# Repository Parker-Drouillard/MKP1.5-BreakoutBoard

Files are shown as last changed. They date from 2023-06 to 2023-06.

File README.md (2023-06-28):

# MKP1.5-BreakoutBoard
A breakout board for supporting dual extrusion &amp; 6 pwm fan control for the Rambo 1.4 

This board supports a Teensy 2.0 slave device to the Rambo 1.4 over Serial. The purpose of this board is to expand the available IO of the Rambo 1.4 to be capable of supporting a dual extrusion system, as well as additional PWM fan controls.

## About this board
This board offers 6 5v fan headers for PWM switching via a darlington array. At this current time, it does not seem the max PWM speed of the Teensy 2.0 is sufficient to run the fans at less than 100% power, so for the time being it is simply a toggle of Off or On.
The board includes a 24V to 5V buck converter, capable of supporting 3A of power, of which only 2A is anticipated to be used. Additionally, 2 ports for PT1000 passthrough, and 2 ports for E3D PT100 Amplifier boards are provided. 
An onboard L298N allows for low voltage switching of 2 independant 24V systems, one of which is being used for the second extruder solenoid, and one will be used in the future fora dynamic extruder pressure motor. Both systems have 2 encontrol pins, 1 for forward, and 1 for reverse.

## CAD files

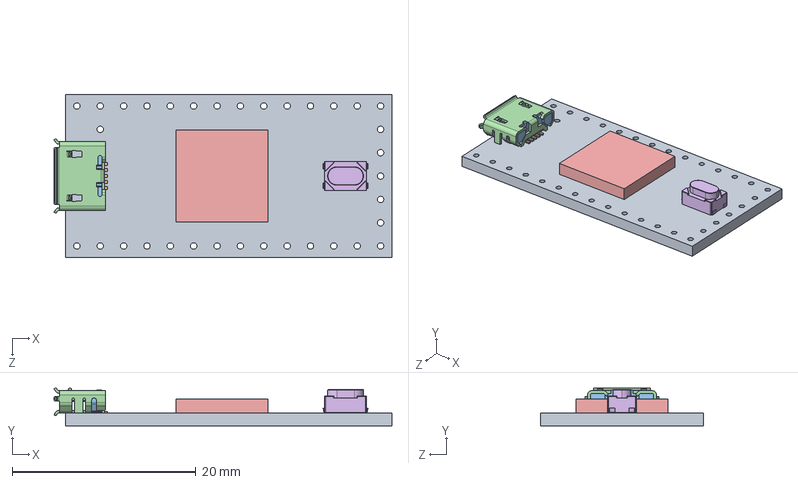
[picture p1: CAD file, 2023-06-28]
teensy.pretty-master/Teensy_4.0_Assembly.STEP
36.8 x 4.12 x 17.7 mm
Teensy_4.0_PCB
Micro USB-B Female 5Pin SMD
NXP iMXRT1062
SKRPACE010 v4

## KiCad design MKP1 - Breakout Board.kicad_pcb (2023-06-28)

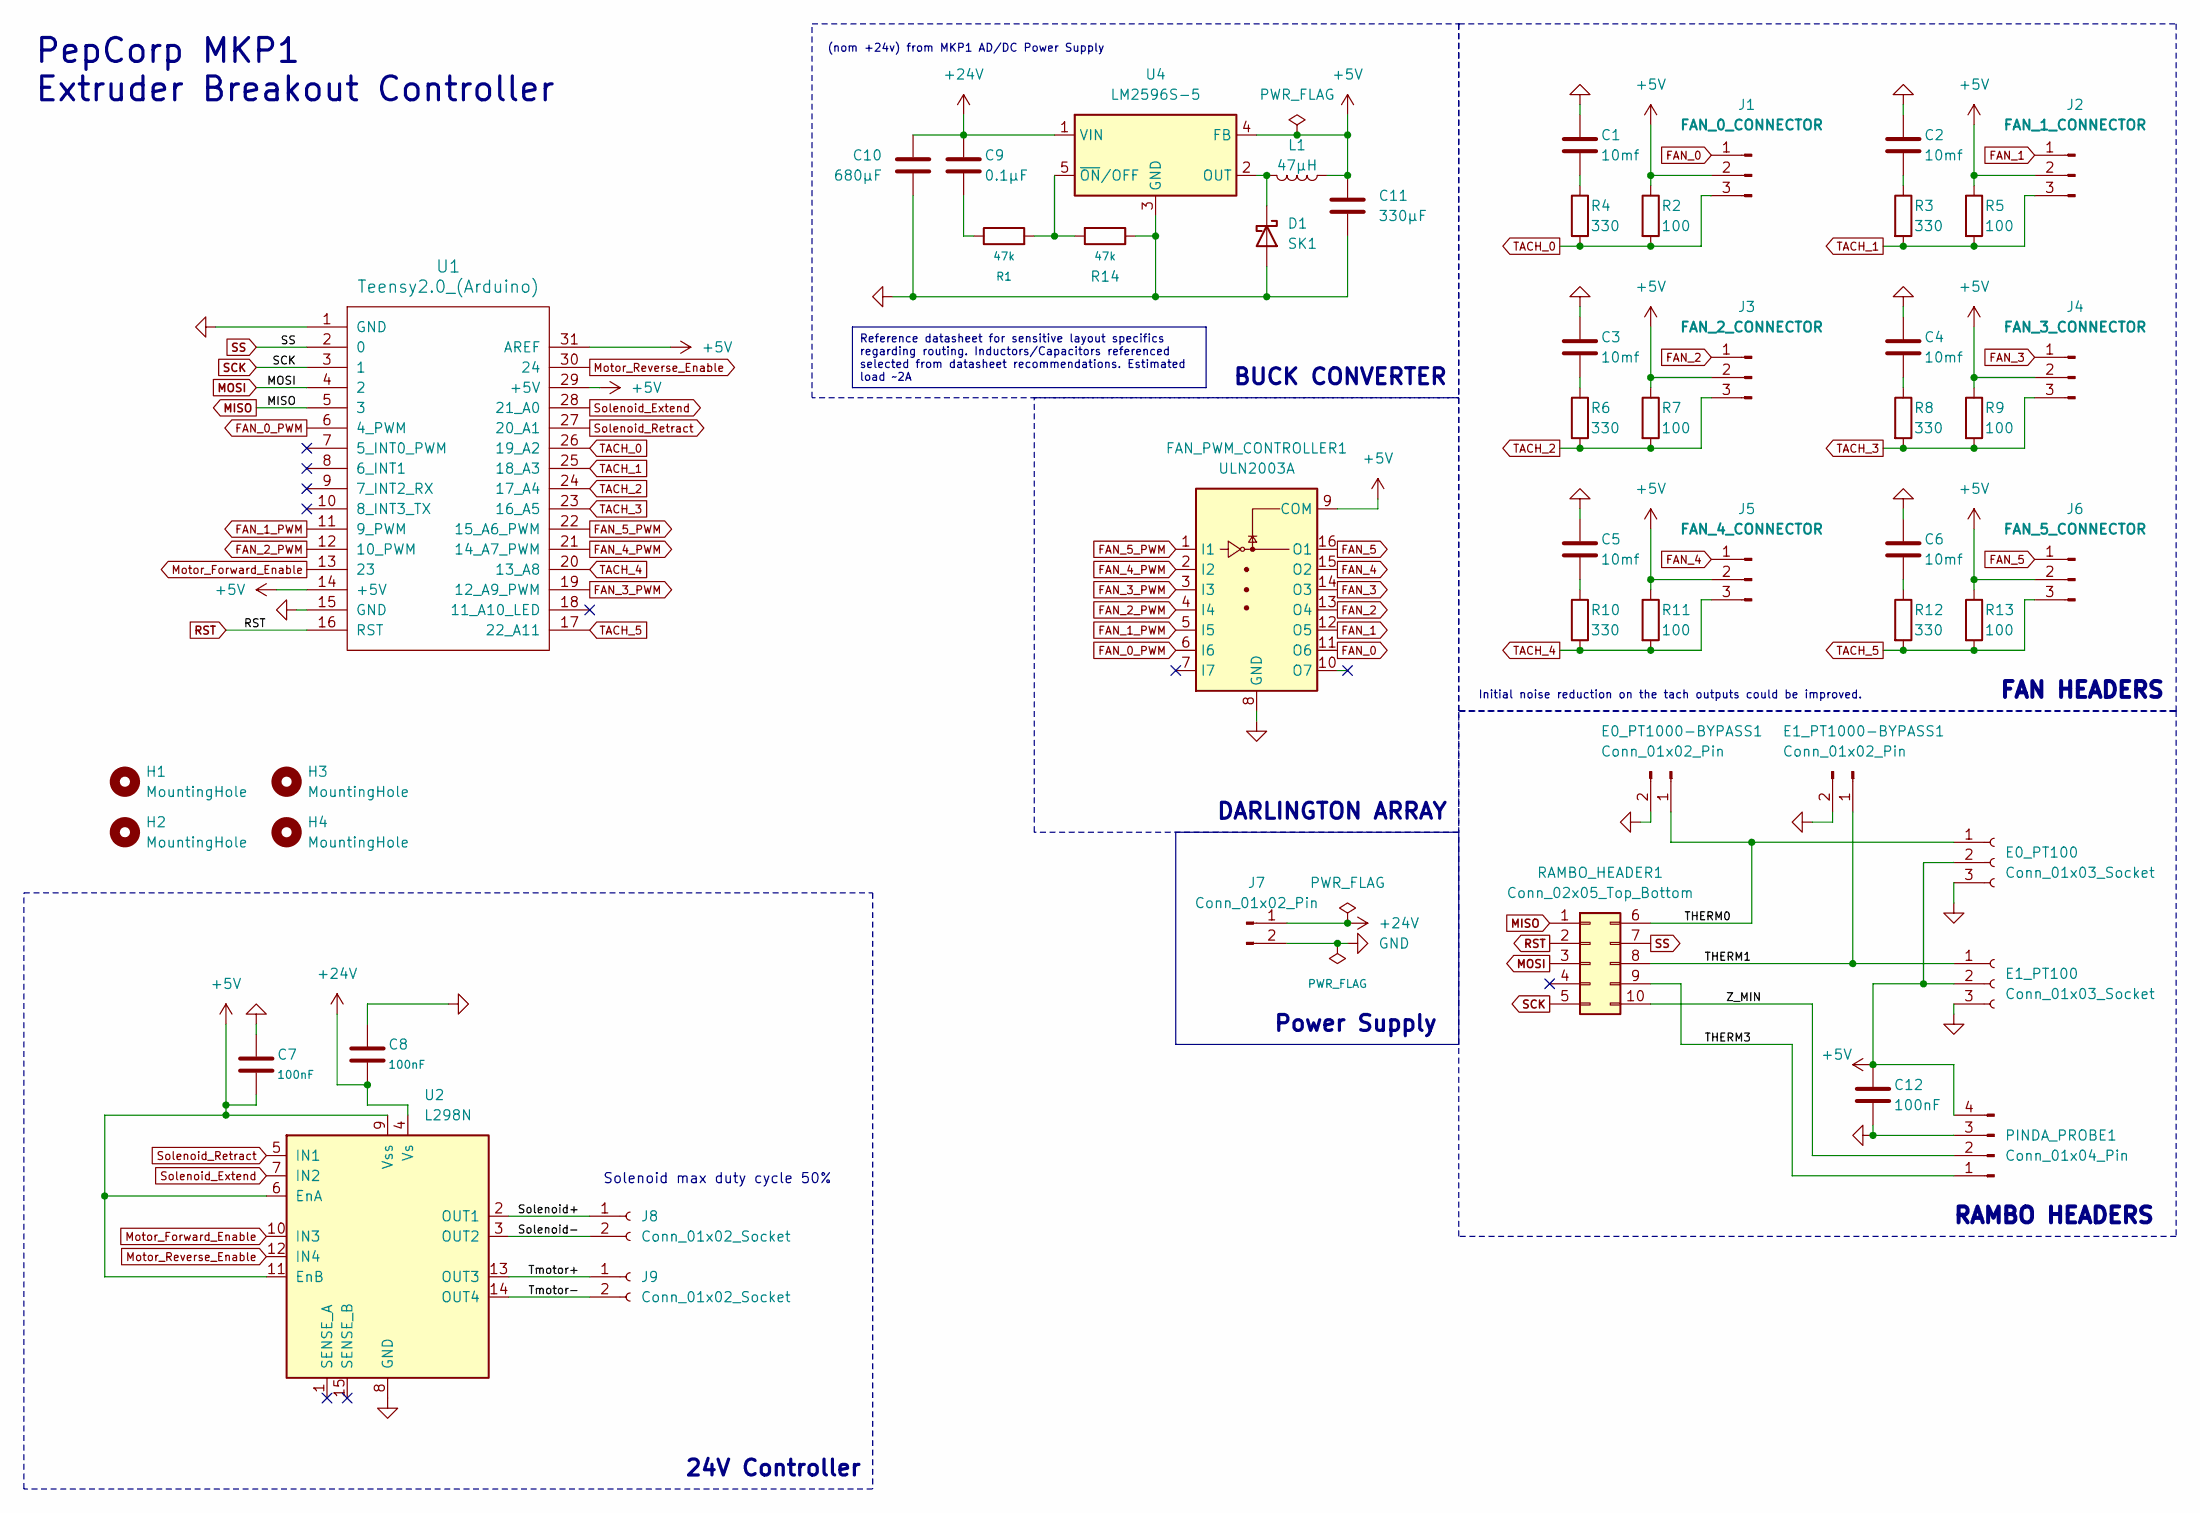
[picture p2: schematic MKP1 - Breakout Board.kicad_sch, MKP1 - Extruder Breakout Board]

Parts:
C1, C2, C3, C4, C5, C6: 10mf; C_0603_1608Metric_Pad1.08x0.95mm_HandSolder
C7, C8, C12: 100nF; C_0402_1005Metric_Pad0.74x0.62mm_HandSolder
C9: 0.1µF; C_0402_1005Metric_Pad0.74x0.62mm_HandSolder
C10: 680µF; C_0603_1608Metric_Pad1.08x0.95mm_HandSolder
C11: 330µF; C_0603_1608Metric_Pad1.08x0.95mm_HandSolder
D1: SK1; D_0603_1608Metric_Pad1.05x0.95mm_HandSolder
E0_PT100, E1_PT100: Conn_01x03_Socket; PinSocket_1x03_P2.00mm_Vertical
E0_PT1000-BYPASS1, E1_PT1000-BYPASS1: Conn_01x02_Pin; Molex_KK-254_AE-6410-02A_1x02_P2.54mm_Vertical
FAN_PWM_CONTROLLER1: ULN2003A; DIP-16_W7.62mm_Socket
H1, H2, H3, H4: MountingHole; MountingHole_3.2mm_M3
J1: FAN_0_CONNECTOR; Molex_KK-396_5273-03A_1x03_P3.96mm_Vertical
J2: FAN_1_CONNECTOR; Molex_KK-396_5273-03A_1x03_P3.96mm_Vertical
J3: FAN_2_CONNECTOR; Molex_KK-396_5273-03A_1x03_P3.96mm_Vertical
J4: FAN_3_CONNECTOR; Molex_KK-396_5273-03A_1x03_P3.96mm_Vertical
J5: FAN_4_CONNECTOR; Molex_KK-396_5273-03A_1x03_P3.96mm_Vertical
J6: FAN_5_CONNECTOR; Molex_KK-396_5273-03A_1x03_P3.96mm_Vertical
J7: Conn_01x02_Pin; Molex_KK-396_A-41791-0002_1x02_P3.96mm_Vertical
J8, J9: Conn_01x02_Socket; Molex_KK-254_AE-6410-02A_1x02_P2.54mm_Vertical
L1: 47µH; L_0402_1005Metric
PINDA_PROBE1: Conn_01x04_Pin; Molex_KK-396_5273-04A_1x04_P3.96mm_Vertical
R1, R14: 47k; R_0402_1005Metric
R2, R5, R7, R9, R11, R13: 100; R_0402_1005Metric
R3, R4, R6, R8, R10, R12: 330; R_0402_1005Metric
RAMBO_HEADER1: Conn_02x05_Top_Bottom; PinHeader_2x05_P2.00mm_Vertical
U1: Teensy2.0_(Arduino); Teensy2.0
U2: L298N; TO-220-15_P2.54x2.54mm_StaggerOdd_Lead4.58mm_Vertical
U4: LM2596S-5; TO-263-5_TabPin3

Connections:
+5V: C7.2, C11.1, C12.1, E0_PT100.2, E1_PT100.2, FAN_PWM_CONTROLLER1.9 (COM), J1.2, J2.2, J3.2, J4.2, J5.2, J6.2, L1.2, PINDA_PROBE1.4, R2.1, R5.1, R7.1, R9.1, R11.1, R13.1, U1.14 (+5V), U1.29 (+5V), U1.31 (AREF), U2.6 (EnA), U2.9 (Vss), U2.11 (EnB), U4.4 (FB); also elsewhere on the board
+24V: C8.2, C9.1, C10.2, J7.1, U2.4 (Vs), U4.1 (VIN)
/Solenoid+: J8.1, U2.2 (OUT1)
/Solenoid-: J8.2, U2.3 (OUT2)
/THERM0: E0_PT100.1, E0_PT1000-BYPASS1.1, RAMBO_HEADER1.6; also elsewhere on the board
/THERM1: E1_PT100.1, E1_PT1000-BYPASS1.1, RAMBO_HEADER1.8; also elsewhere on the board
/THERM3: PINDA_PROBE1.1, RAMBO_HEADER1.9; also elsewhere on the board
/Tmotor+: J9.1, U2.13 (OUT3)
/Tmotor-: J9.2, U2.14 (OUT4)
/Z_MIN: PINDA_PROBE1.2, RAMBO_HEADER1.10; also elsewhere on the board
FAN_0: FAN_PWM_CONTROLLER1.11 (O6), J1.1
FAN_0_PWM: FAN_PWM_CONTROLLER1.6 (I6), U1.6 (4_PWM)
FAN_1: FAN_PWM_CONTROLLER1.12 (O5), J2.1
FAN_1_PWM: FAN_PWM_CONTROLLER1.5 (I5), U1.11 (9_PWM)
FAN_2: FAN_PWM_CONTROLLER1.13 (O4), J3.1
FAN_2_PWM: FAN_PWM_CONTROLLER1.4 (I4), U1.12 (10_PWM)
FAN_3: FAN_PWM_CONTROLLER1.14 (O3), J4.1
FAN_3_PWM: FAN_PWM_CONTROLLER1.3 (I3), U1.19 (12_A9_PWM)
FAN_4: FAN_PWM_CONTROLLER1.15 (O2), J5.1
FAN_4_PWM: FAN_PWM_CONTROLLER1.2 (I2), U1.21 (14_A7_PWM)
FAN_5: FAN_PWM_CONTROLLER1.16 (O1), J6.1
FAN_5_PWM: FAN_PWM_CONTROLLER1.1 (I1), U1.22 (15_A6_PWM)
GND: C1.1, C2.1, C3.1, C4.1, C5.1, C6.1, C7.1, C8.1, C10.1, C11.2, C12.2, D1.2 (A), E0_PT100.3, E0_PT1000-BYPASS1.2, E1_PT100.3, E1_PT1000-BYPASS1.2, FAN_PWM_CONTROLLER1.8 (GND), J7.2, PINDA_PROBE1.3, R14.1, U1.1 (GND), U1.15 (GND), U2.8 (GND), U4.3 (GND); also elsewhere on the board
MISO: RAMBO_HEADER1.1, U1.5 (3)
MOSI: RAMBO_HEADER1.3, U1.4 (2)
Motor_Forward_Enable: U1.13 (23), U2.10 (IN3)
Motor_Reverse_Enable: U1.30 (24), U2.12 (IN4)
unnamed: C1.2, R4.1
unnamed: C2.2, R3.1
unnamed: C3.2, R6.1
unnamed: C4.2, R8.1
unnamed: C5.2, R10.1
unnamed: C6.2, R12.1
unnamed: C9.2, R1.1
unnamed: D1.1 (K), L1.1, U4.2 (OUT)
unnamed: R1.2, R14.2, U4.5 (~ON/OFF)
RST: RAMBO_HEADER1.2, U1.16 (RST)
SCK: RAMBO_HEADER1.5, U1.3 (1)
SS: RAMBO_HEADER1.7, U1.2 (0)
Solenoid_Extend: U1.28 (21_A0), U2.7 (IN2)
Solenoid_Retract: U1.27 (20_A1), U2.5 (IN1)
TACH_0: J1.3, R2.2, R4.2, U1.26 (19_A2)
TACH_1: J2.3, R3.2, R5.2, U1.25 (18_A3)
TACH_2: J3.3, R6.2, R7.2, U1.24 (17_A4)
TACH_3: J4.3, R8.2, R9.2, U1.23 (16_A5)
TACH_4: J5.3, R10.2, R11.2, U1.20 (13_A8)
TACH_5: J6.3, R12.2, R13.2, U1.17 (22_A11)

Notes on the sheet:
Reference datasheet for sensitive layout specifics regarding routing. Inductors/Capacitors referenced selected from datasheet recommendations. Estimated load ~2A
FAN HEADERS
DARLINGTON ARRAY
Solenoid max duty cycle 50%
Initial noise reduction on the tach outputs could be improved.
(nom +24v) from MKP1 AD/DC Power Supply
Power Supply
PepCorp MKP1 Extruder Breakout Controller
24V Controller
BUCK CONVERTER
RAMBO HEADERS

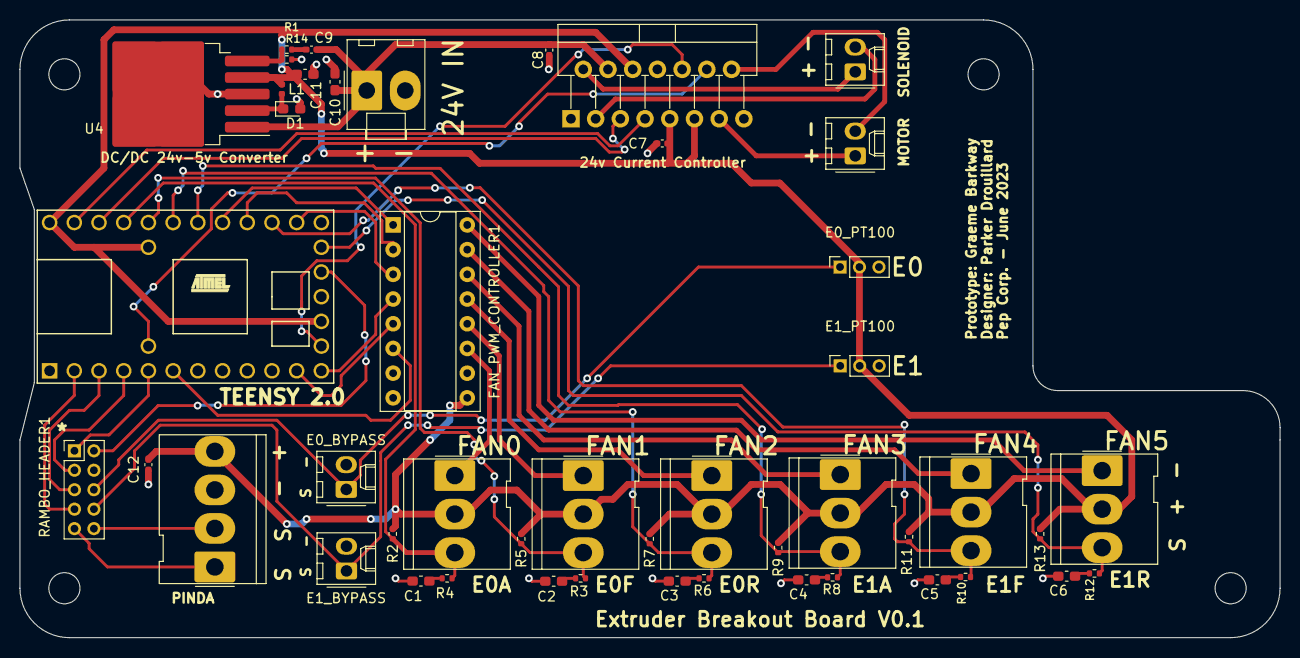
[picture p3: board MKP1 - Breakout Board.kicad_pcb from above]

Board: 2 copper layers, 129.5 x 63.5 mm, 51 parts (0 on the bottom side), 47 nets.

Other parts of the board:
E0_BYPASS, E1_BYPASS: Conn_01x02_Pin; Molex_KK-254_AE-6410-02A_1x02_P2.54mm_Vertical
PINDA: Conn_01x04_Pin; Molex_KK-396_5273-04A_1x04_P3.96mm_Vertical

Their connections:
+5V: PINDA.4; also elsewhere on the board
/THERM0: E0_BYPASS.1; also elsewhere on the board
/THERM1: E1_BYPASS.1; also elsewhere on the board
/THERM3: PINDA.1; also elsewhere on the board
/Z_MIN: PINDA.2; also elsewhere on the board
GND: E0_BYPASS.2, E1_BYPASS.2, PINDA.3; also elsewhere on the board
